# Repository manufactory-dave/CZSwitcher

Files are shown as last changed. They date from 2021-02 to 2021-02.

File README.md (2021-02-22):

# CZSwitcher

====Cube Zero Switcher Project====

Version 1
Board revisions:

Distro Rev 0
Carriage Rev 0
Tool Rev 0

====Overview====

This is the project data store for the Cube Zero custom electronics. Why Cube Zero? Because that film came after Cube 2 Hypercube, and it was a better film.

The Cube Zero is my 3D printer design, essentially a Hypercube/HEVort inspired thing that features a cable-less tool changing system, because outlandish expense and complication is king. My intent is not to have airtight documentation here, as that will kill progress on the project. Please do submit questions via whatever method github suggests best, I have relatively little experience with the platform.

Three seperate KiCad v5 projects are stored here:

Distroboard: The heart of the electronics - this takes a common stepper motor input and 3 separate fan/heater/thermistor channels, bed probing and well as 3 auxilliary channels and routes them to a 20 way 1mm pitch FFC.
Designed to interface with a Bigtreetech GTR V1.0, but will probably work with other boards, YMMV.

*Current Ratings*
Heaters - 3.5A per channel, max 30V
Fans - 1A per channel, routed via Aux 1
Auxilliary channels - 1A per channel, max 24V
Thermistors - currently designed to interface directly with the GTR thermistors. A 3V3 connection is required for at least one thermistor as this supplies power to your Z probe solution of choice.
	Provision has been made to allow these channels to drive thermocouple or PTH amplifiers.
5V in - 1A max
VDC in - 1A max, 30V max
Stepper motor - designed for a TMC2209, with protection circuitry for hot swapping taken from the TMC2209 datasheet. This is not intended and disable stepper commands should be used before swapping motors, however the protection is there just in case.
Probe - low current.

Carriageboard: 3 separate boards.

Carriage Board A:
Breaks out the FFC cable into the 3 aux outputs, a BLTouch connector, an interface for a Precision Piezo V2.85 board and 2 piezo inputs, status LEDs for the heater and probe throughput.

Carriage Board B:
Interfaces with toolhead, provides 2 aux outputs, and repeats status LEDs

LED status board:
For if you need status LEDs somewhere that the above two boards don't help with.

Toolboard: 5 separate boards:
Toolboard A & B ride on the tool, and provide electrical connection to the toolhead and dock. Everything that needs to terminate here to support extruder motors, hot end cooling fans, thermal sense and heating, terminates here.

Dock Interface Board - Takes a high power and data connection from the Distro board, takes a logic input from an external sensor that detects when a tool is removed from the dock and sends it down the data connection to enable that tool over the FFC
Dock LEDs - provides heating and tool select status LEDs for fun/info/making your machine look cool.
Dock Umbilical - connected via FFC to the interface board, provides a mobile connection point to form electrical connections with a docked tool.

====Errors====
There are two known errors:
Carriageboard (no gate resistor on Q2)
Toolboard (Q2 Source and Drain reversed)

====BOM====
The BOM is sketchy, once it's defined and working I'll update it. For now it has several errors and parts I already owned do not have part numbers attached.

====PCBs====
Not available at this time

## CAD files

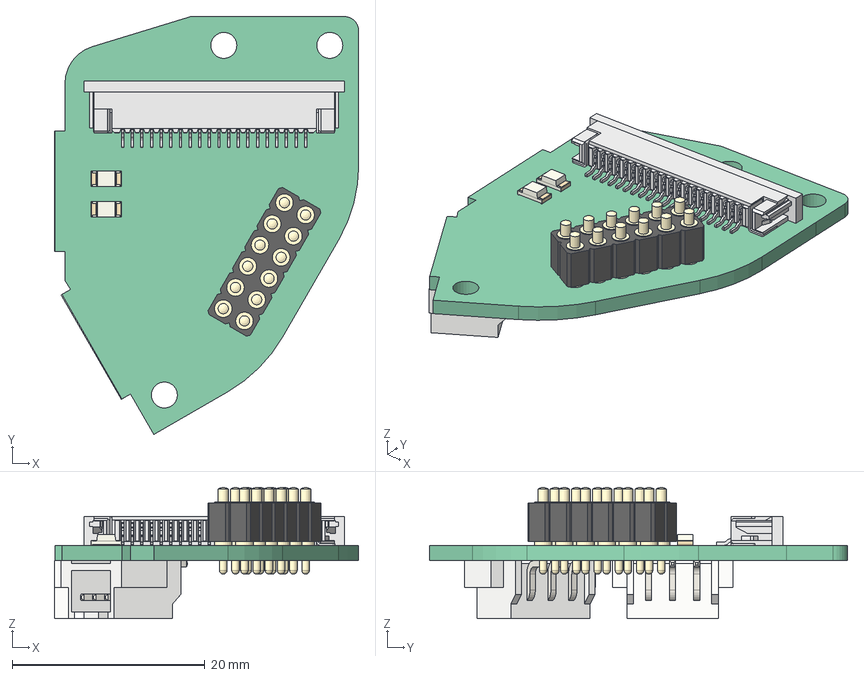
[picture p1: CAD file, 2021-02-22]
carriageboards/toolpost_board_final.step
31.6 x 43.4 x 13.6 mm
Local_CS_be1
Pcb_be1
PCB_Sketch_be1
J14_813-S1-012-10-014_5FF84852
J11_ZF1-20-01-T-WT-TR001_5FFBF43E
D6_LED_1206_3216Metric_5FFBFFB6 x 2
J12_JST-XH_SMT_1x3_5FFBF74F x 2

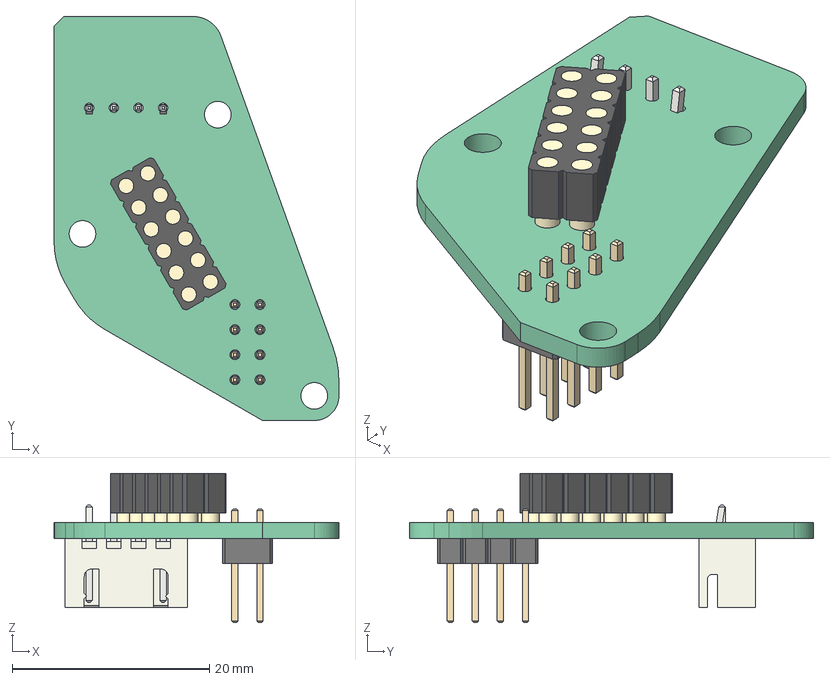
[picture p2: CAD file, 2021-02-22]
toolboards/toolhead_interface_pcb_v1.step
28.9 x 41.0 x 15.1 mm
Local_CS_7721
Pcb_7721
PCB_Sketch_7721
J0_802-10-012-30-507101_60049A0C
J1_JST_B4B_XH_A_5FFDFDDD
J2_PinHeader_2x04_P254mm_Vertical_6002294E

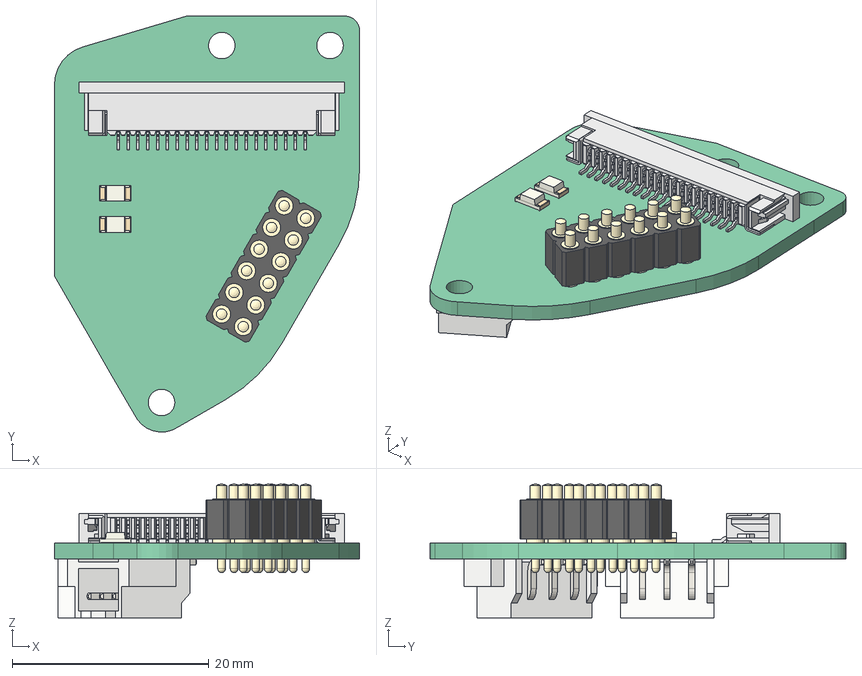
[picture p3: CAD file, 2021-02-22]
carriageboards/toolpost_board_v1.step
31.0 x 42.3 x 13.6 mm
Local_CS_be1
Pcb_be1
PCB_Sketch_be1
J14_813-S1-012-10-014_5FF84852
J11_ZF1-20-01-T-WT-TR001_5FFBF43E
D6_LED_1206_3216Metric_5FFBFFB6 x 2
J12_JST-XH_SMT_1x3_5FFBF74F x 2

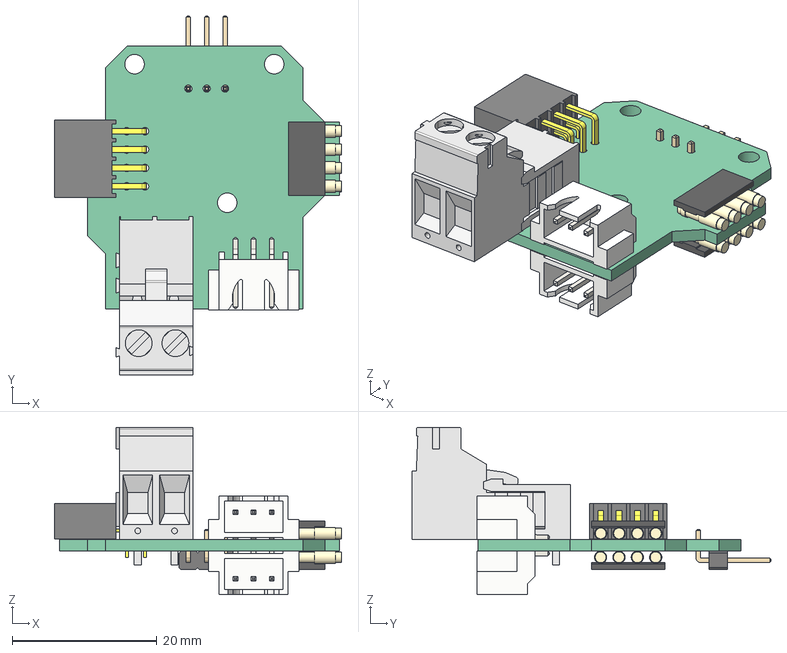
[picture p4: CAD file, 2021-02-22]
toolboards/toolhead_plug_pcb_v10.step
39.7 x 49.6 x 23.1 mm
Local_CS_6657
Pcb_6657
PCB_Sketch_6657
J3_ssw-104-02-g-d-ra_6009D480
J8_8MM-11-004-02-131_600C5BE0 x 2
J5_C-282815-2_600C5B60
J5_C-282807-2_600C5B60[2]
J6_JST-XH_SMT_1x3_6009D3B3 x 2
JP0_PinHeader_1x03_P254mm_Horizontal_6009D4DE

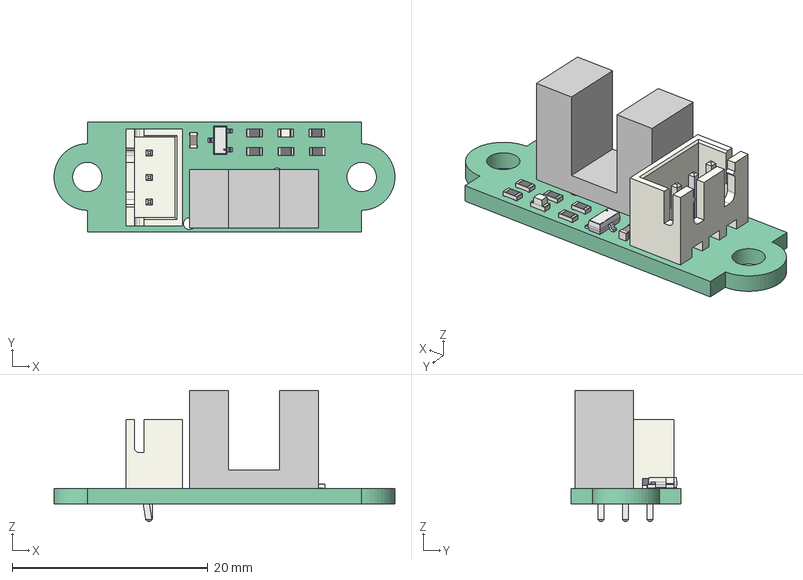
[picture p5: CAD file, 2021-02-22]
toolboards/opto_endstop.step
34.8 x 11.2 x 13.4 mm
Local_CS_877e
Pcb_877e
PCB_Sketch_877e
U1_Opto_Switch_60112675
R5_R_0603_1608Metric_60112659 x 5
Q1_FDV304P_60112A24
J1_JST_B3B_XH_A_601125EE
D1_LED_0603_1608Metric_60112815
C1_C_0603_1608Metric_601129B8

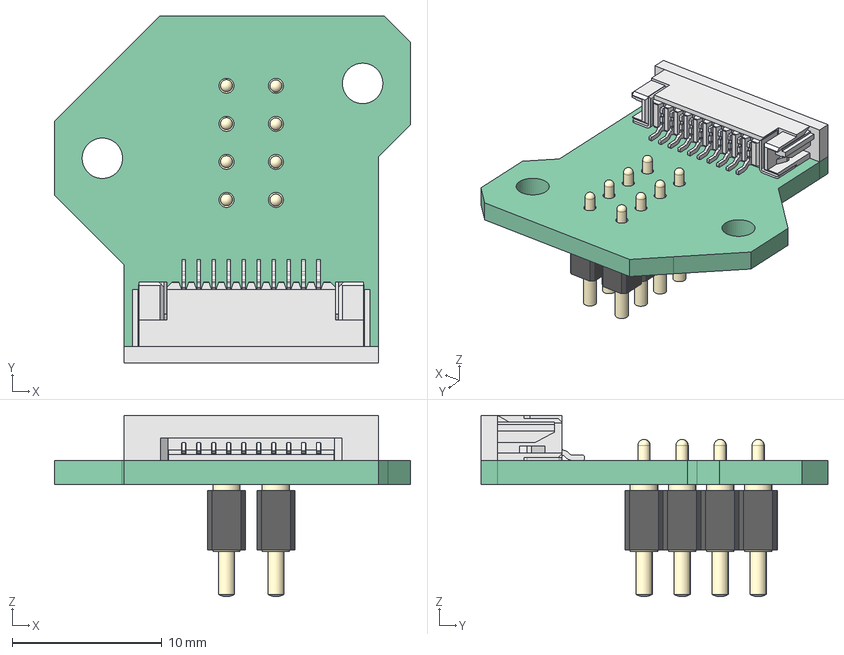
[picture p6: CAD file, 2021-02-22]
toolboards/umbilical_pcb_v5.step
23.8 x 23.2 x 12.1 mm
Local_CS_6006
Pcb_6006
PCB_Sketch_6006
J10_ZF1-10-01-T-WT-TR001_60089AD0
J11_811-S1-004-10-017_600CD6DF x 2

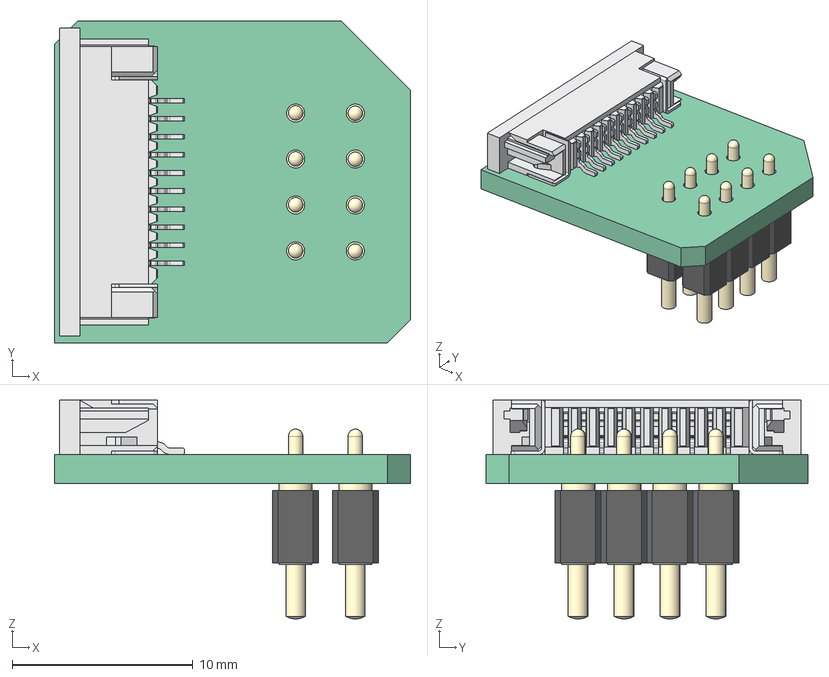
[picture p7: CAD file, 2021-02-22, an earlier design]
toolboards/umbilical_pcb_v3.step
19.7 x 17.8 x 12.1 mm
Local_CS_c0
Pcb_c0
PCB_Sketch_c0
J10_ZF1-10-01-T-WT-TR001_60089AD0
J11_811-S1-004-10-017_600CD6DF x 2

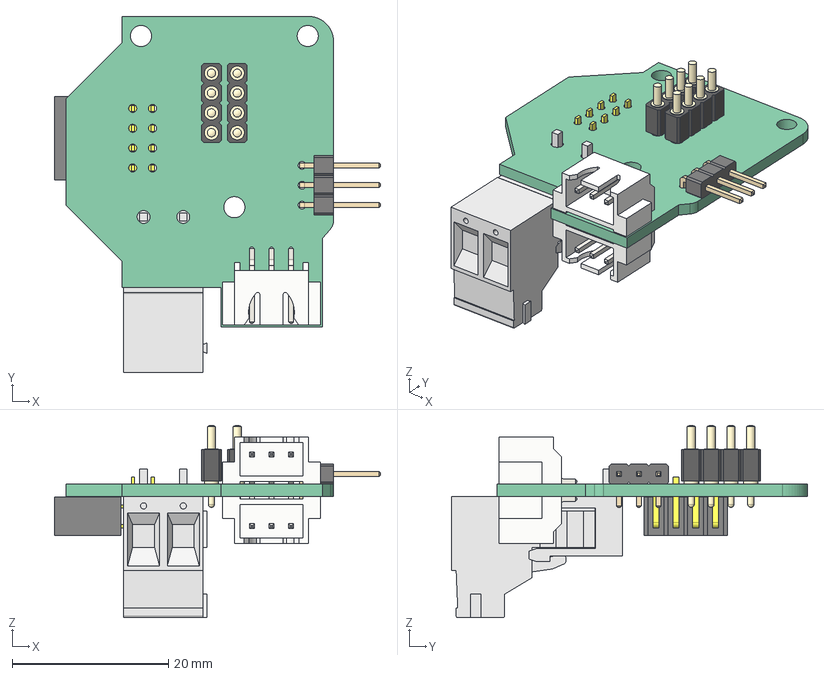
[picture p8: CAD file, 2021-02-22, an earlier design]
toolboards/toolhead_plug_pcb_v1.step
41.7 x 45.6 x 24.6 mm
Local_CS_4742
Pcb_4742
PCB_Sketch_4742
J8_811-S1-004-10-017_6005AF96 x 2
JP0_PinHeader_1x03_P254mm_Horizontal_6005AD56
J4_JST-XH_SMT_1x3_6005AE06 x 2
J3_ssw-104-02-g-d-ra_6005AFCC
J5_C-282815-2_6005AF65
J5_C-282807-2_6005AF65[2]

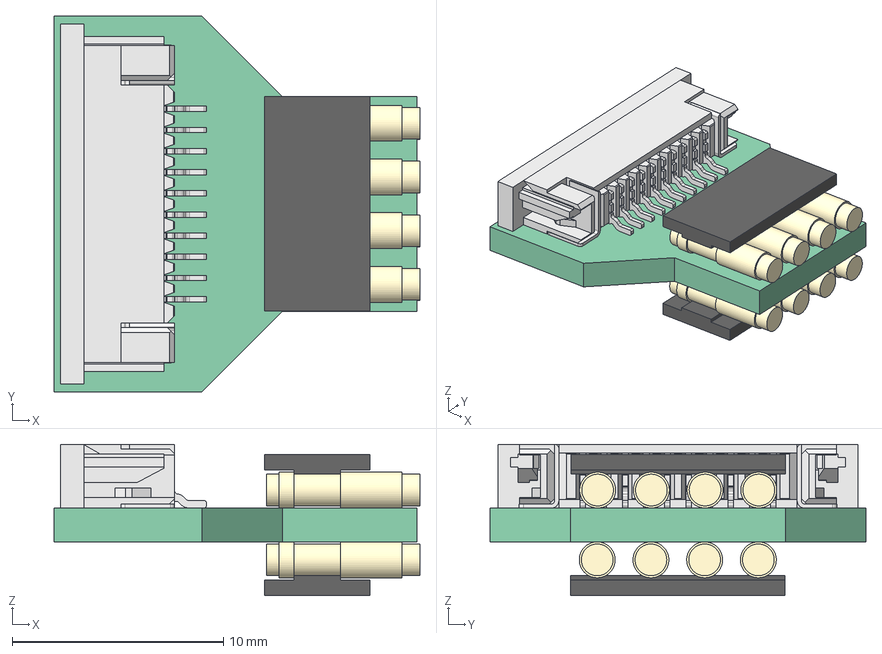
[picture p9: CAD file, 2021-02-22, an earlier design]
toolboards/umbilical_pcb_v2.step
17.3 x 17.8 x 7.15 mm
Local_CS_10e1
Pcb_10e1
PCB_Sketch_10e1
J10_ZF1-10-01-T-WT-TR001_60089AD0
J9_8MM-11-004-02-131_600627A0 x 2

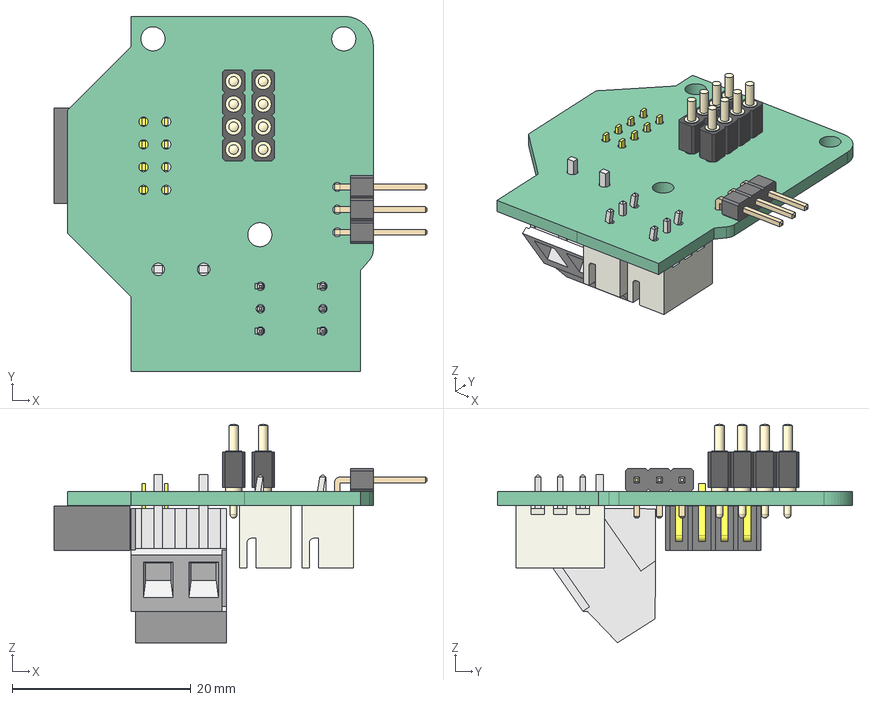
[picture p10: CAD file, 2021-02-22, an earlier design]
toolboards/toolhead_plug_pcb_v3.step
41.7 x 39.7 x 24.4 mm
Local_CS_25a3
Pcb_25a3
PCB_Sketch_25a3
JP0_PinHeader_1x03_P254mm_Horizontal_6005AD56
J8_811-S1-004-10-017_6005AF96 x 2
J5_C-282847-2_6005AF65
J6_JST_B3B_XH_A_60053BFE x 2
J3_ssw-104-02-g-d-ra_6005AFCC

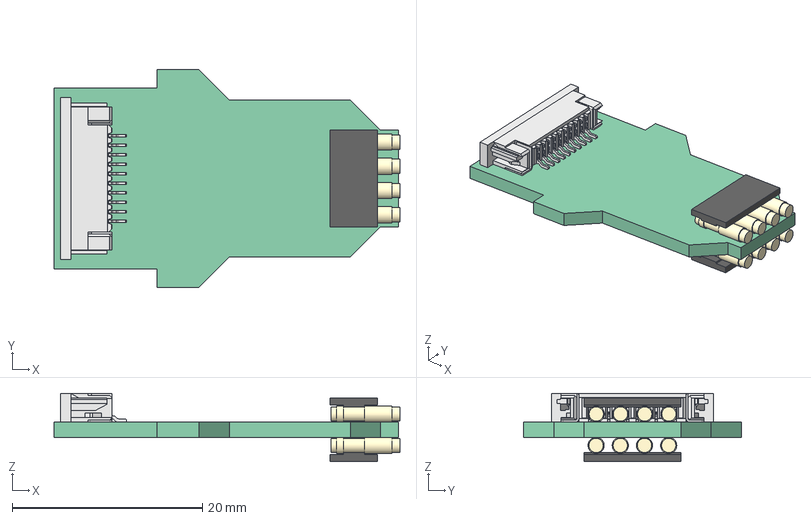
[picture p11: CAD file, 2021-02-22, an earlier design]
toolboards/umbilical_pcb_v1.step
36.3 x 22.9 x 7.15 mm
Local_CS_2082
Pcb_2082
PCB_Sketch_2082
J10_ZF1-10-01-T-WT-TR001_600627BD
J11_8MM-11-004-02-131_60063E7D x 2

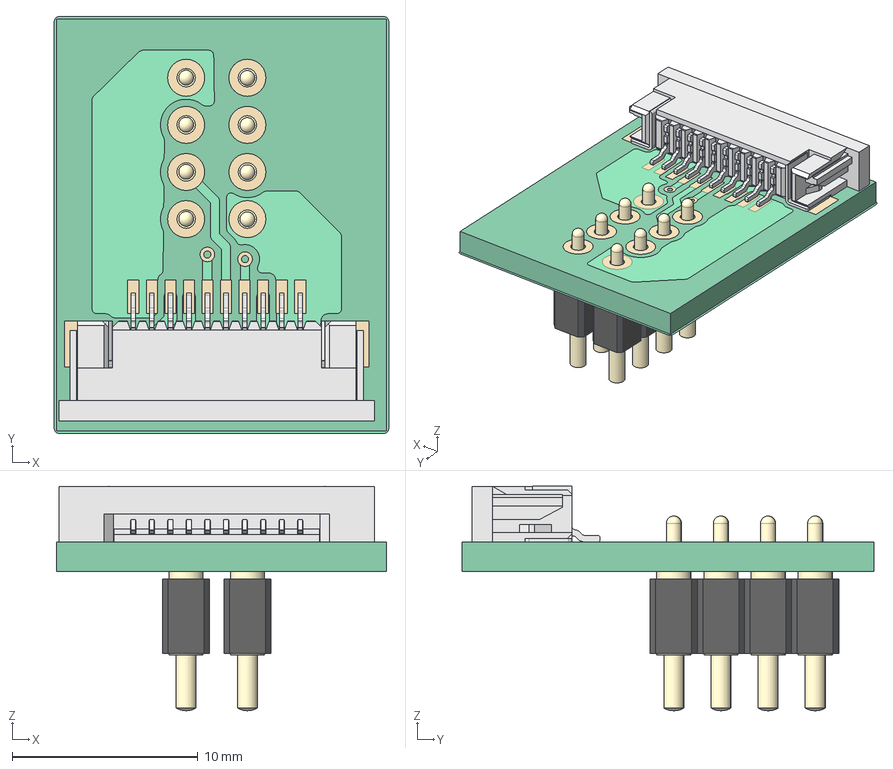
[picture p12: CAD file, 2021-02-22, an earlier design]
toolboards/umbilical_pcb_v4.step
18.0 x 22.5 x 12.1 mm
Local_CS_7027
Pcb_7027
PCB_Sketch_7027
topTracks_7027
botTracks_7027
J10_ZF1-10-01-T-WT-TR001_60089AD0
J11_811-S1-004-10-017_600CD6DF x 2

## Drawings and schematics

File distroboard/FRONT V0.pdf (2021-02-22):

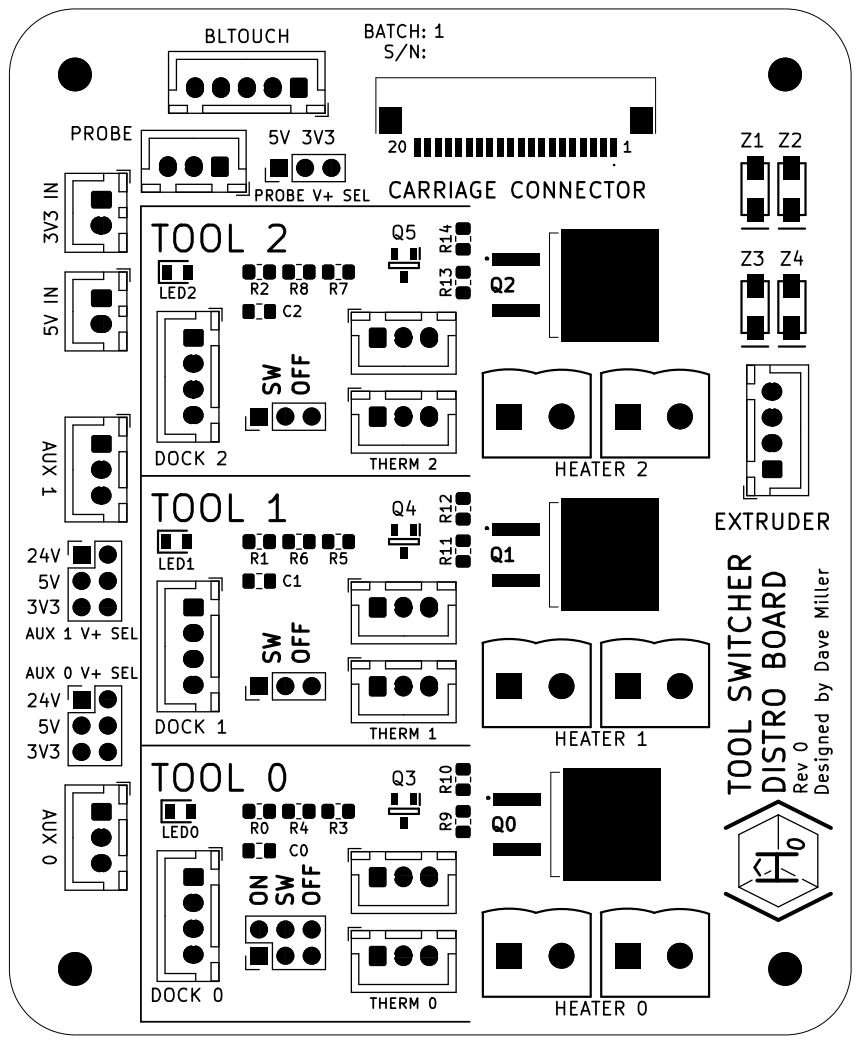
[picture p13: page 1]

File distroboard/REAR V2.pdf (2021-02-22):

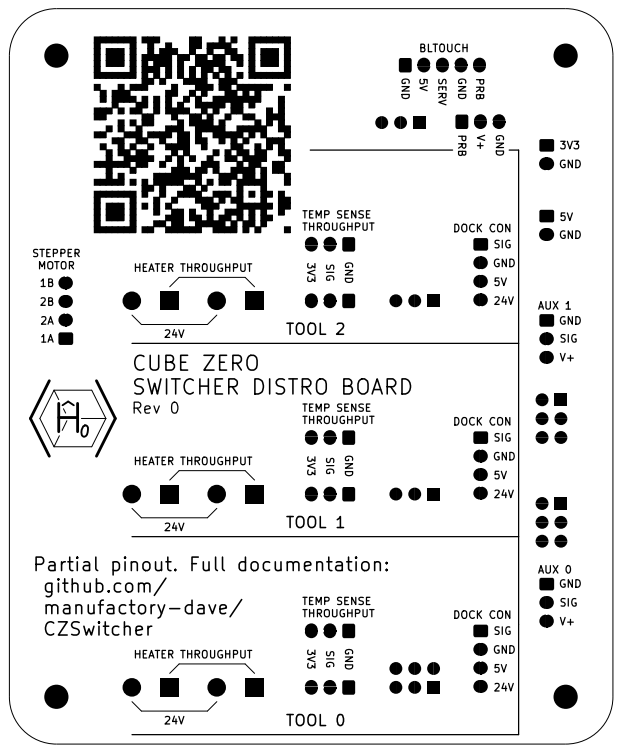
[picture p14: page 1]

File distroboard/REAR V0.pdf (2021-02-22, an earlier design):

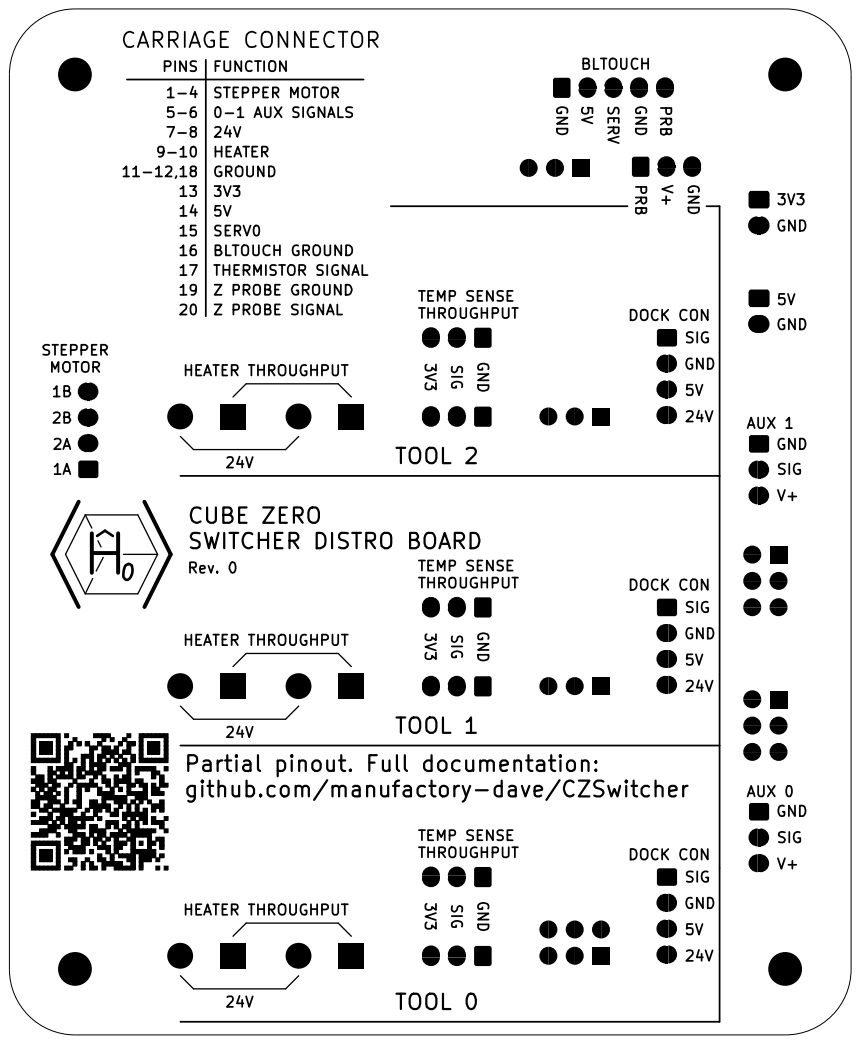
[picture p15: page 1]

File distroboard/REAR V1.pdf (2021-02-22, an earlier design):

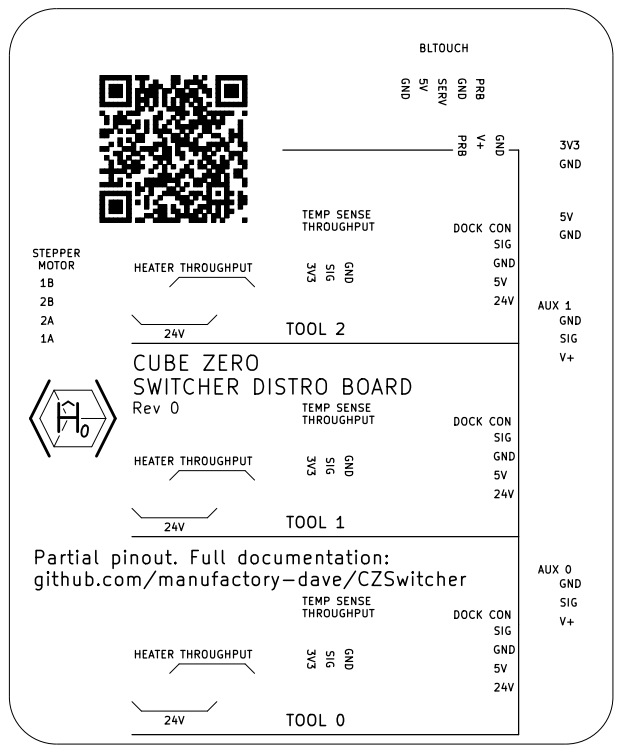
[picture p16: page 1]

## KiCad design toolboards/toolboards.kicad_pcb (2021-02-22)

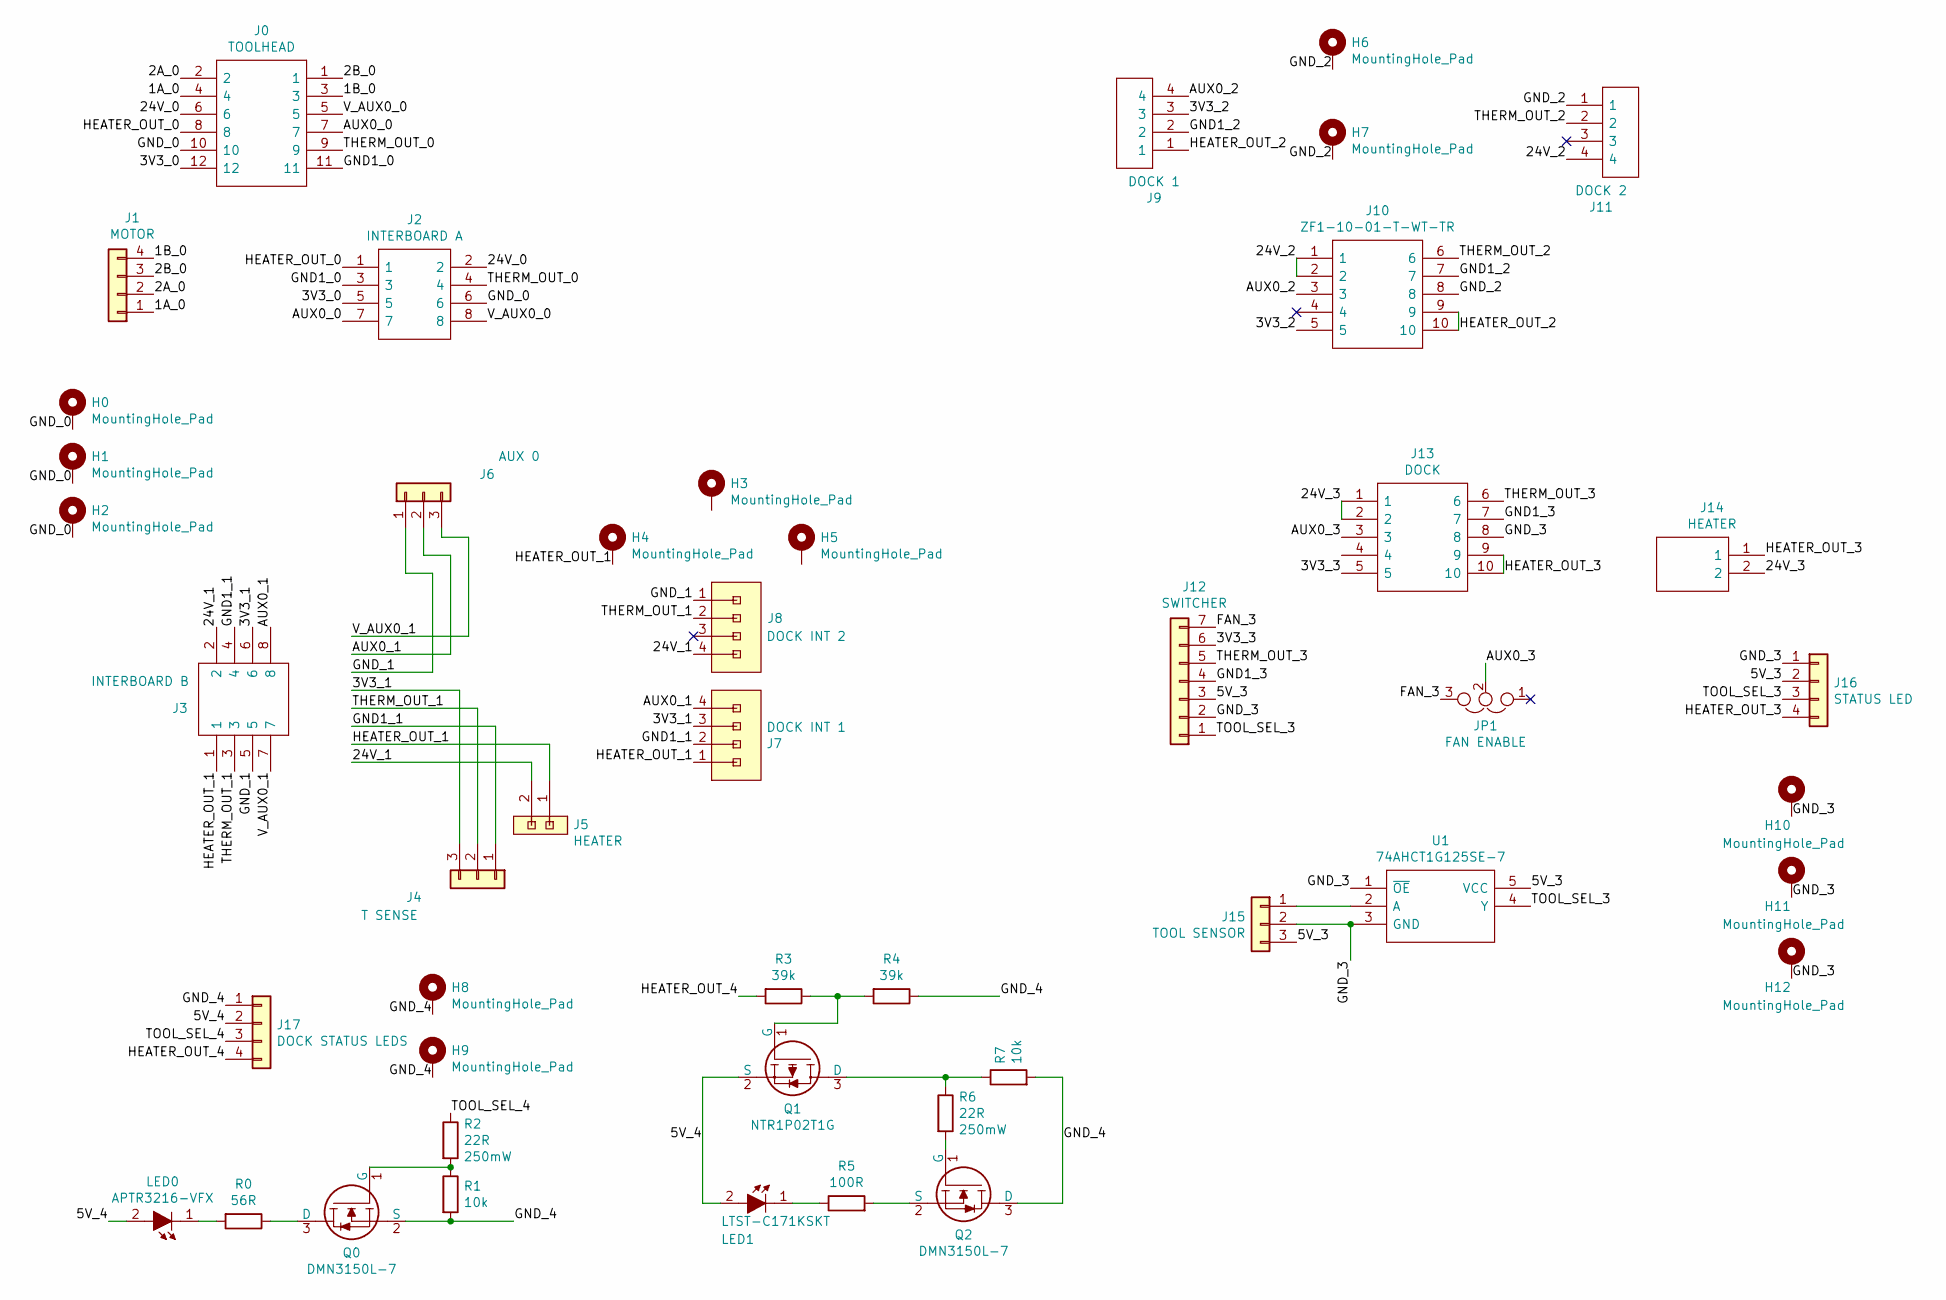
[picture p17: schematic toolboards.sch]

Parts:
H0, H1, H2, H3, H4, H5: MountingHole_Pad; MountingHole_2.7mm_M2.5_DIN965_Pad_TopBottom
H6, H7, H8, H9, H10, H11, H12: MountingHole_Pad; MountingHole_3.2mm_M3_DIN965_Pad_TopBottom
J0: TOOLHEAD; 8021001230507101_HS; Manufacturer_Part_Number 802-10-012-30-507101
J1: MOTOR; JST_XH_B4B-XH-A_1x04_P2.50mm_Vertical
J2: INTERBOARD A; HDRV8W64P254_2X4_1016X495X838P; Manufacturer_Part_Number TSW-104-07-T-D
J3: INTERBOARD B; SSW-104-XX-YYY-D-RA; Manufacturer_Part_Number SSW-104-02-T-D-RA
J4: T SENSE; JST-XH_2.50MM_03x01_SMT; Manufacturer_Part_Number S3B-XH-SM4-TB(LF)(SN)
J5, J14: HEATER; SHDRRA2W102P0X508_1X2_1016X1200X850P; Manufacturer_Part_Number 282815-2
J6: AUX 0; JST-XH_2.50MM_03x01_SMT; Manufacturer_Part_Number S3B-XH-SM4-TB(LF)(SN)
J7: DOCK INT 1; 8MM11000402131_handsolder
J8: DOCK INT 2; 8MM11000402131_handsolder
J9: DOCK 1; 811-S1-004-10-017101; Mouser Part Number 437-8MM11000402131
J10: ZF1-10-01-T-WT-TR; ZF1-10-XX-ZZ-WT_Handsolder; Manufacturer_Part_Number ZF1-10-01-T-WT-TR
J11: DOCK 2; 811-S1-004-10-017101; Mouser Part Number 437-8MM11000402131
J12: SWITCHER; JST_XH_B7B-XH-A_1x07_P2.50mm_Vertical
J13: DOCK; ZF1-10-XX-ZZ-WT_Handsolder; Manufacturer_Part_Number ZF1-10-01-T-WT-TR
J15: TOOL SENSOR; JST_XH_B3B-XH-A_1x03_P2.50mm_Vertical
J16: STATUS LED; JST-ZH_S4B-ZR-SM4A-TF; Part Number S4B-ZR-SM4A-TF
J17: DOCK STATUS LEDS; JST-ZH_S4B-ZR-SM4A-TF; Part Number S4B-ZR-SM4A-TF
JP1: FAN ENABLE; PinHeader_1x03_P2.54mm_Vertical
LED0: APTR3216-VFX; LED_1206_3216Metric_Pad1.42x1.75mm_HandSolder; Manufacturer_Part_Number APTR3216-VFX
LED1: LTST-C171KSKT; LED_0805_2012Metric_Pad1.15x1.40mm_HandSolder; Manufacturer_Part_Number LTST-C171KSKT
Q0, Q2: DMN3150L-7; SUPER-SOT-3; Manufacturer_Part_Number DMN3150L-7
Q1: NTR1P02T1G; SUPER-SOT-3; Manufacturer_Part_Number NTR1P02T1G
R0: 56R; R_0805_2012Metric_Pad1.20x1.40mm_HandSolder; Manufacturer_Part_Number RK73B2ATTD560J
R1, R7: 10k; R_0805_2012Metric_Pad1.20x1.40mm_HandSolder; Manufacturer_Part_Number RK73B2ATTE103J
R2, R6: 22R; R_0805_2012Metric_Pad1.20x1.40mm_HandSolder; Manufacturer_Part_Number RK73B2ATTDD220J
R3: 39k; R_0805_2012Metric_Pad1.20x1.40mm_HandSolder; Manufacturer_Part_Number RK73B2ATTE393J
R4: 39k; R_0805_2012Metric_Pad1.20x1.40mm_HandSolder; Manufacturer_Part_Number RK73B2ATTE103J
R5: 100R; R_0805_2012Metric_Pad1.20x1.40mm_HandSolder; Manufacturer_Part_Number RK73B2ATTE101J
U1: 74AHCT1G125SE-7; SOT-23-5_HandSoldering; Manufacturer_Part_Number 74AHCT1G125SE-7

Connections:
/1A_0: J0.4, J1.1
/1B_0: J0.3, J1.4
/2A_0: J0.2, J1.2
/2B_0: J0.1, J1.3
/3V3_0: J0.12, J2.5
/3V3_1: J3.6, J4.3, J7.3
/3V3_2: J9.3, J10.5
/3V3_3: J12.6, J13.5
/5V_3: J12.3, J15.3, J16.2, U1.5 (VCC)
/5V_4: J17.2, LED0.2, LED1.2, Q1.2 (S)
/24V_0: J0.6, J2.2
/24V_1: J3.2, J4.4, J4.5, J5.2, J8.4
/24V_2: J10.1, J10.2, J11.4
/24V_3: J13.1, J13.2, J14.2
/AUX0_0: J0.7, J2.7
/AUX0_1: J3.8, J6.2, J7.4
/AUX0_2: J9.4, J10.3
/AUX0_3: J13.3, JP1.2
/FAN_3: J12.7, JP1.3
/GND1_0: J0.11, J2.3
/GND1_1: J3.4, J4.1, J7.2
/GND1_2: J9.2, J10.7
/GND1_3: J12.4, J13.7
/GND_0: H0.1, H1.1, H2.1, J0.10, J2.6
/GND_1: J3.5, J6.1, J8.1
/GND_2: H6.1, H7.1, J10.8, J10.11, J10.12, J11.1
/GND_3: H10.1, H11.1, H12.1, J12.2, J13.8, J15.2, J16.1, U1.1 (~OE), U1.3 (GND)
/GND_4: H8.1, H9.1, J17.1, Q0.2 (S), Q2.3 (D), R1.2, R4.1, R7.2
/HEATER_OUT_0: J0.8, J2.1
/HEATER_OUT_1: H4.1, J3.1, J5.1, J7.1
/HEATER_OUT_2: J9.1, J10.9, J10.10
/HEATER_OUT_3: J13.9, J13.10, J14.1, J16.4
/HEATER_OUT_4: J17.4, R3.2
/THERM_OUT_0: J0.9, J2.4
/THERM_OUT_1: J3.3, J4.2, J8.2
/THERM_OUT_2: J10.6, J11.2
/THERM_OUT_3: J12.5, J13.6
/TOOL_SEL_3: J12.1, J16.3, U1.4 (Y)
/TOOL_SEL_4: J17.3, R2.1
/V_AUX0_0: J0.5, J2.8
/V_AUX0_1: J3.7, J6.3
unnamed: J15.1, U1.2 (A)
unnamed: LED0.1, R0.2
unnamed: LED1.1, R5.1
unnamed: Q0.1 (G), R1.1, R2.2
unnamed: Q0.3 (D), R0.1
unnamed: Q1.1 (G), R3.1, R4.2
unnamed: Q1.3 (D), R6.1, R7.1
unnamed: Q2.1 (G), R6.2
unnamed: Q2.2 (S), R5.2

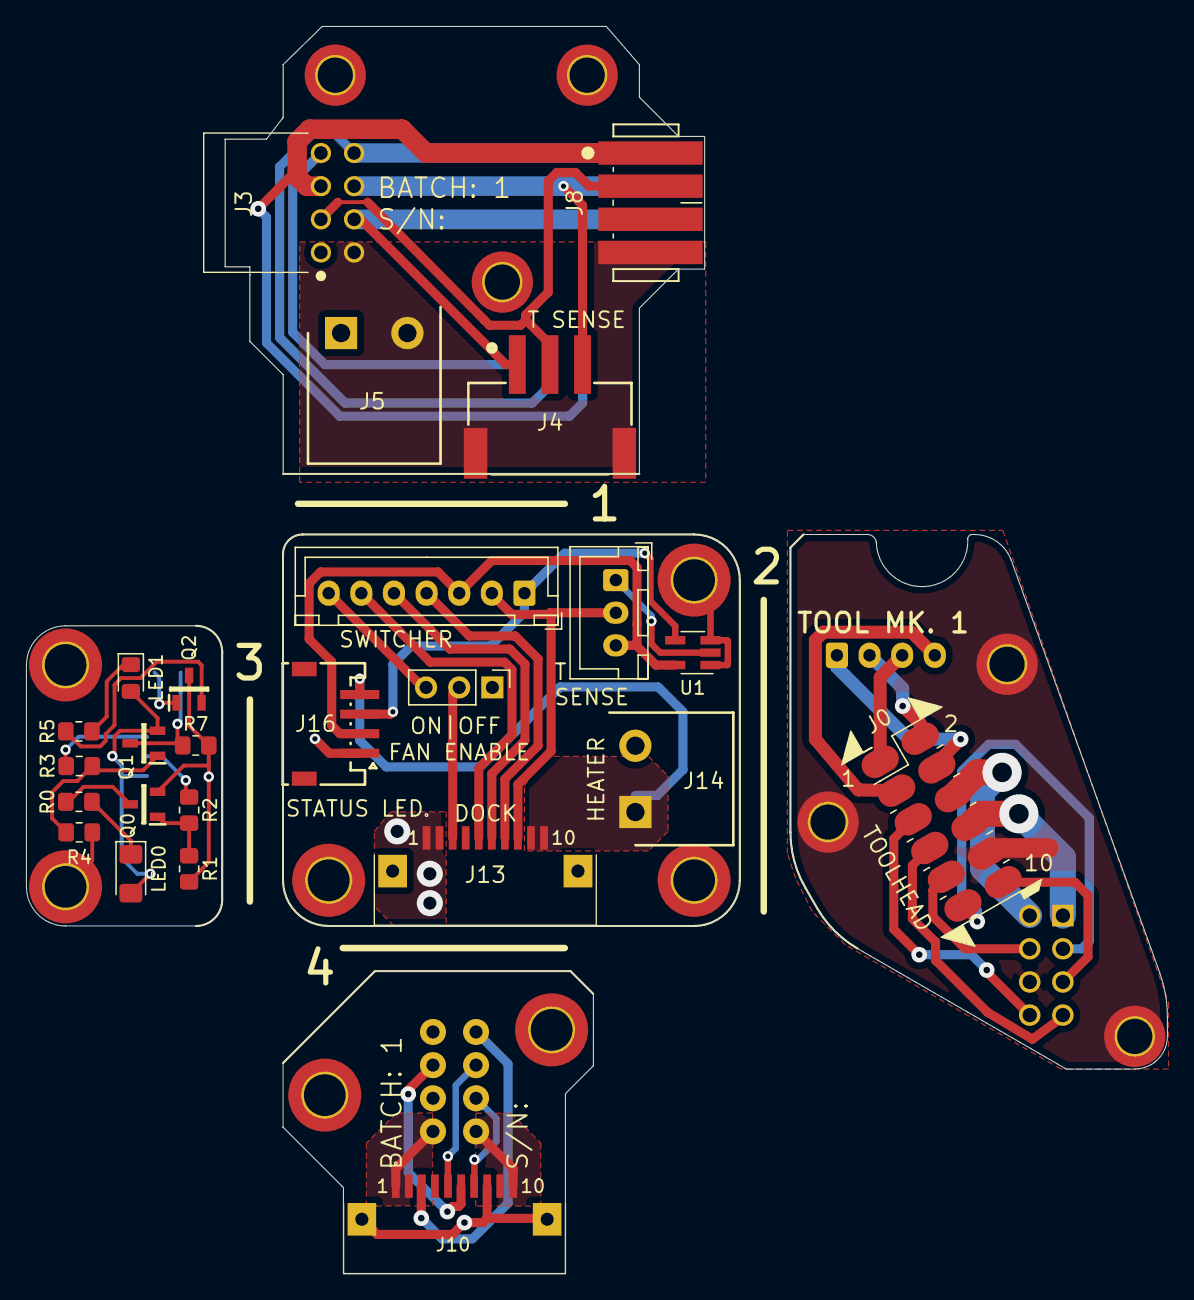
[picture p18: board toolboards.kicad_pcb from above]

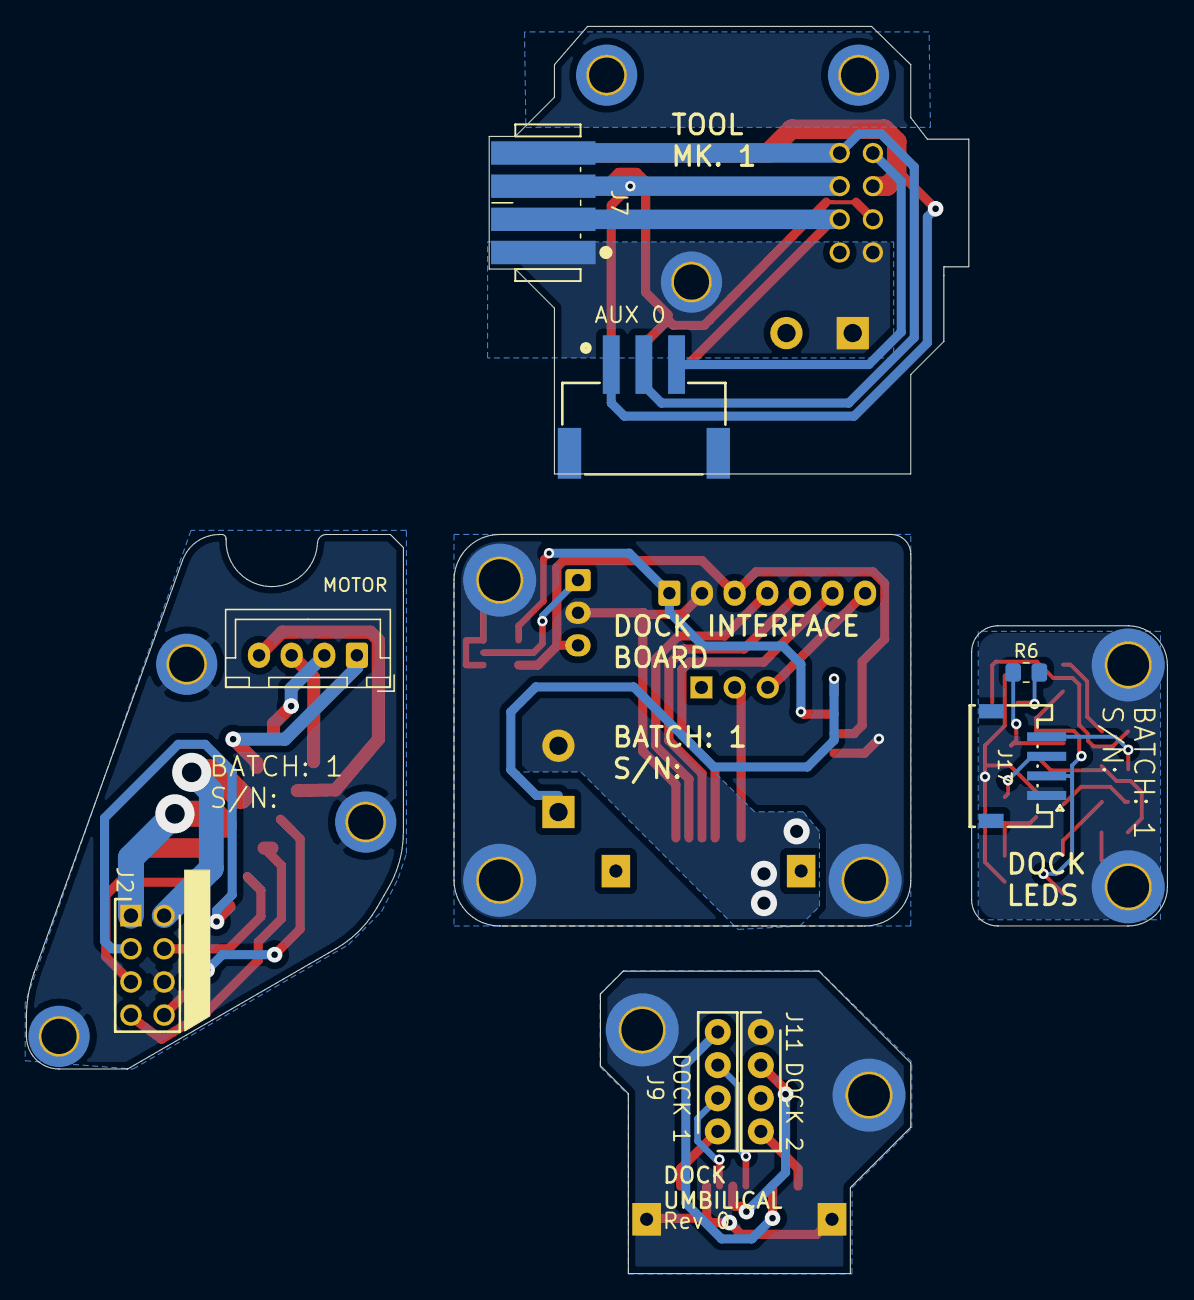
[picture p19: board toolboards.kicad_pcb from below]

Board: 2 copper layers, 87.4 x 95.6 mm, 46 parts (8 on the bottom side), 50 nets.

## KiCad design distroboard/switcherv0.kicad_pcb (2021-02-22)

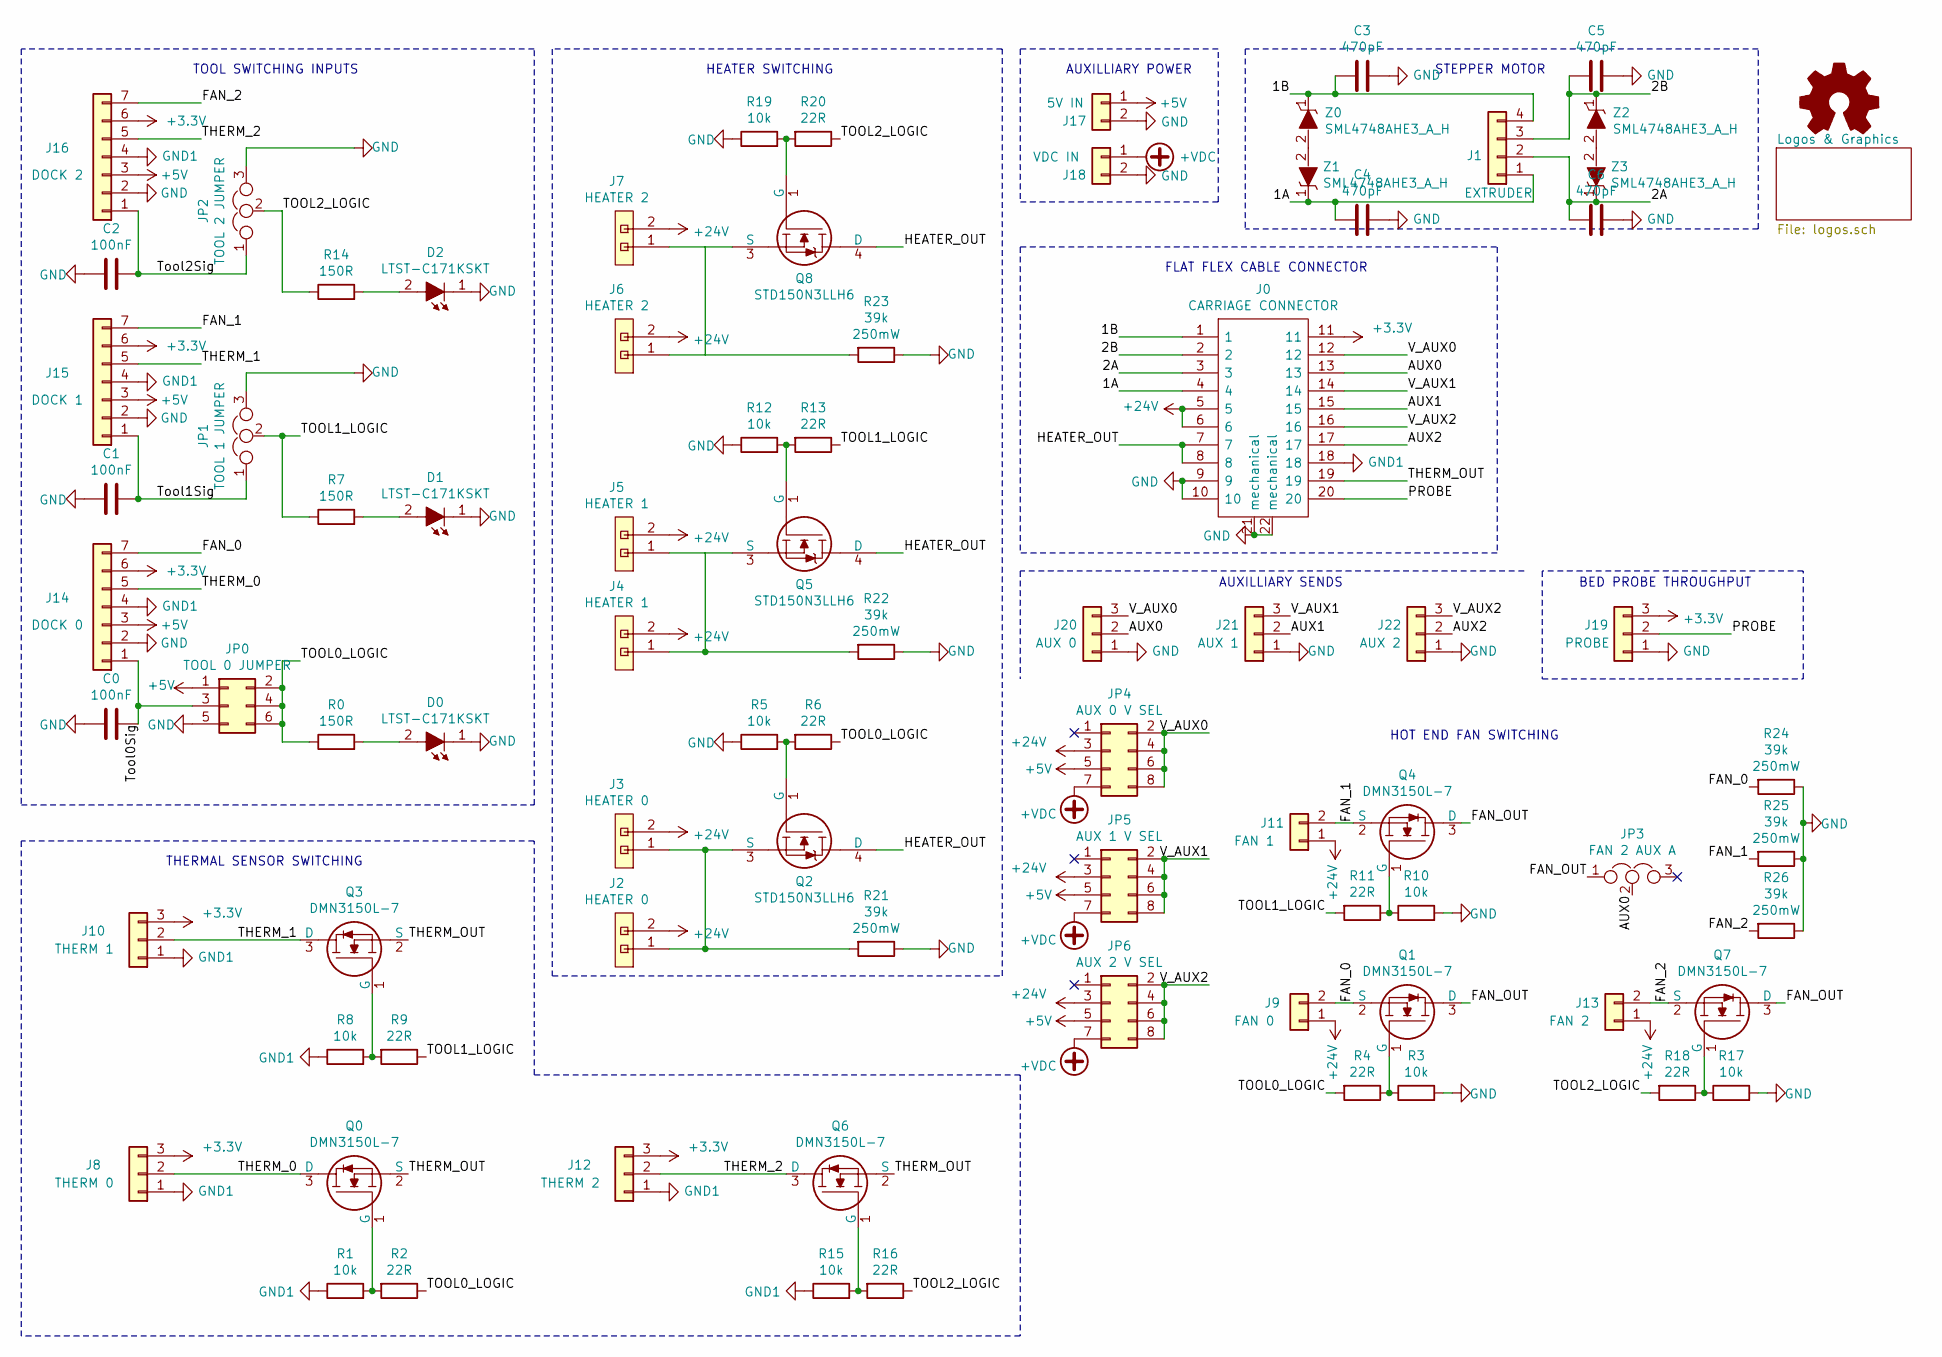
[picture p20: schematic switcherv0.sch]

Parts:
C0, C1, C2: 100nF; C_0805_2012Metric_Pad1.18x1.45mm_HandSolder; Manufacturer_Part_Number 08051C103KAT2A
C3, C4, C5, C6: 470pF; C_0805_2012Metric_Pad1.18x1.45mm_HandSolder; Manufacturer_Part_Number C0805C471J1GACTU
D0, D1, D2: LTST-C171KSKT; LED_0805_2012Metric_Pad1.15x1.40mm_HandSolder; Manufacturer_Part_Number LTST-C171KSKT
J0: CARRIAGE CONNECTOR; ZF1-20-XX-ZZ-WT; Manufacturer_Part_Number ZF1-20-01-T-WT
J1: EXTRUDER; JST_XH_B4B-XH-A_1x04_P2.50mm_Vertical
J2, J3: HEATER 0; SHDR2W102P0X508_1X2_1016X835X1230P; Manufacturer_Part_Number 282824-2
J4, J5: HEATER 1; SHDR2W102P0X508_1X2_1016X835X1230P; Manufacturer_Part_Number 282824-2
J6, J7: HEATER 2; SHDR2W102P0X508_1X2_1016X835X1230P; Manufacturer_Part_Number 282824-2
J8: THERM 0; JST_XH_B3B-XH-A_1x03_P2.50mm_Vertical
J9: FAN 0; JST_XH_B2B-XH-A_1x02_P2.50mm_Vertical
J10: THERM 1; JST_XH_B3B-XH-A_1x03_P2.50mm_Vertical
J11: FAN 1; JST_XH_B2B-XH-A_1x02_P2.50mm_Vertical
J12: THERM 2; JST_XH_B3B-XH-A_1x03_P2.50mm_Vertical
J13: FAN 2; JST_XH_B2B-XH-A_1x02_P2.50mm_Vertical
J14: DOCK 0; JST_XH_B7B-XH-A_1x07_P2.50mm_Vertical
J15: DOCK 1; JST_XH_B7B-XH-A_1x07_P2.50mm_Vertical
J16: DOCK 2; JST_XH_B7B-XH-A_1x07_P2.50mm_Vertical
J17: 5V IN; JST_XH_B2B-XH-A_1x02_P2.50mm_Vertical
J18: VDC IN; JST_XH_B2B-XH-A_1x02_P2.50mm_Vertical
J19: PROBE; JST_XH_B3B-XH-A_1x03_P2.50mm_Vertical
J20: AUX 0; JST_XH_B3B-XH-A_1x03_P2.50mm_Vertical
J21: AUX 1; JST_XH_B3B-XH-A_1x03_P2.50mm_Vertical
J22: AUX 2; JST_XH_B3B-XH-A_1x03_P2.50mm_Vertical
JP0: TOOL 0 JUMPER; PinHeader_2x03_P2.54mm_Vertical
JP1: TOOL 1 JUMPER; PinHeader_1x03_P2.54mm_Vertical
JP2: TOOL 2 JUMPER; PinHeader_1x03_P2.54mm_Vertical
JP3: FAN 2 AUX A; PinHeader_1x03_P2.54mm_Vertical
JP4: AUX 0 V SEL; PinHeader_2x04_P1.27mm_Vertical; Manufacturer_Part_Number M50-055023W0445
JP5: AUX 1 V SEL; PinHeader_2x04_P1.27mm_Vertical; Manufacturer_Part_Number M50-055023W0445
JP6: AUX 2 V SEL; PinHeader_2x04_P1.27mm_Vertical; Manufacturer_Part_Number M50-055023W0445
LOGO2: Logo_Open_Hardware_Small; OSHW-Symbol_8.9x8mm_Copper
Q0, Q1, Q3, Q4, Q6, Q7: DMN3150L-7; SUPER-SOT-3; Manufacturer_Part_Number DMN3150L-7
Q2, Q5, Q8: STD150N3LLH6; TO228P972X240-3N; Manufacturer_Part_Number STD150N3LLH6
R0, R7, R14: 150R; R_0805_2012Metric_Pad1.20x1.40mm_HandSolder; Manufacturer_Part_Number RK73B2ATTE151J
R1, R3, R5, R8, R10, R12, R15, R17, R19: 10k; R_0805_2012Metric_Pad1.20x1.40mm_HandSolder; Manufacturer_Part_Number RK73B2ATTE103J
R2, R4, R6, R9, R11, R13, R16, R18, R20: 22R; R_0805_2012Metric_Pad1.20x1.40mm_HandSolder; Manufacturer_Part_Number RK73B2ATTDD220J
R21, R22, R23, R24, R25, R26: 39k; R_0805_2012Metric_Pad1.20x1.40mm_HandSolder; Manufacturer_Part_Number RK73B2ATTD393J
Z0, Z1, Z2, Z3: SML4748AHE3_A_H; DIOM5127X229N; Mouser Part Number 78-SML4748AHE3_A/H

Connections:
+3V3: J0.11, J8.3, J10.3, J12.3, J14.6, J15.6, J16.6, J19.3
+5V: J14.3, J15.3, J16.3, J17.1, JP0.1, JP4.5, JP5.5, JP6.5
+24V: J0.5, J0.6, J2.2, J3.2, J4.2, J5.2, J6.2, J7.2, J9.1, J11.1, J13.1, JP4.3, JP5.3, JP6.3
+VDC: J18.1, JP4.7, JP5.7, JP6.7
/1A: C4.2, J0.4, J1.1, Z1.1
/1B: C3.2, J0.1, J1.4, Z0.1
/2A: C6.2, J0.3, J1.2, Z3.1
/2B: C5.2, J0.2, J1.3, Z2.1
/AUX0: J0.13, J20.2, JP3.2
/AUX1: J0.15, J21.2
/AUX2: J0.17, J22.2
/FAN_0: J9.2, J14.7, Q1.2 (S), R24.2
/FAN_1: J11.2, J15.7, Q4.2 (S), R25.2
/FAN_2: J13.2, J16.7, Q7.2 (S), R26.2
/FAN_OUT: JP3.1, Q1.3 (D), Q4.3 (D), Q7.3 (D)
/HEATER_OUT: J0.7, J0.8, Q2.4 (D), Q5.4 (D), Q8.4 (D)
/PROBE: J0.20, J19.2
/THERM_0: J8.2, J14.5, Q0.3 (D)
/THERM_1: J10.2, J15.5, Q3.3 (D)
/THERM_2: J12.2, J16.5, Q6.3 (D)
/THERM_OUT: J0.19, Q0.2 (S), Q3.2 (S), Q6.2 (S)
/TOOL0_LOGIC: JP0.2, JP0.4, JP0.6, R0.1, R2.1, R4.2, R6.1
/TOOL1_LOGIC: JP1.2, R7.1, R9.1, R11.2, R13.1
/TOOL2_LOGIC: JP2.2, R14.1, R16.1, R18.2, R20.1
/Tool0Sig: C0.1, J14.1, JP0.3
/Tool1Sig: C1.1, J15.1, JP1.1
/Tool2Sig: C2.1, J16.1, JP2.1
/V_AUX0: J0.12, J20.3, JP4.2, JP4.4, JP4.6, JP4.8
/V_AUX1: J0.14, J21.3, JP5.2, JP5.4, JP5.6, JP5.8
/V_AUX2: J0.16, J22.3, JP6.2, JP6.4, JP6.6, JP6.8
GND: C0.2, C1.2, C2.2, C3.1, C4.1, C5.1, C6.1, D0.1, D1.1, D2.1, J0.9, J0.10, J0.21 (mechanical), J0.22 (mechanical), J14.2, J15.2, J16.2, J17.2, J18.2, J19.1, J20.1, J21.1, J22.1, JP0.5, JP1.3, JP2.3, R3.2, R5.1, R10.2, R12.1, R17.2, R19.1, R21.1, R22.1, R23.1, R24.1, R25.1, R26.1; also elsewhere on the board
GND1: J0.18, J8.1, J10.1, J12.1, J14.4, J15.4, J16.4, R1.1, R8.1, R15.1
unnamed: D0.2, R0.2
unnamed: D1.2, R7.2
unnamed: D2.2, R14.2
unnamed: J2.1, J3.1, Q2.3 (S), R21.2
unnamed: J4.1, J5.1, Q5.3 (S), R22.2
unnamed: J6.1, J7.1, Q8.3 (S), R23.2
unnamed: Q0.1 (G), R1.2, R2.2
unnamed: Q1.1 (G), R3.1, R4.1
unnamed: Q2.1 (G), R5.2, R6.2
unnamed: Q3.1 (G), R8.2, R9.2
unnamed: Q4.1 (G), R10.1, R11.1
unnamed: Q5.1 (G), R12.2, R13.2
unnamed: Q6.1 (G), R15.2, R16.2
unnamed: Q7.1 (G), R17.1, R18.1
unnamed: Q8.1 (G), R19.2, R20.2
unnamed: Z0.2, Z1.2
unnamed: Z2.2, Z3.2

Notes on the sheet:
TOOL SWITCHING INPUTS
HEATER SWITCHING
THERMAL SENSOR SWITCHING
AUXILLIARY POWER
FLAT FLEX CABLE CONNECTOR
AUXILLIARY SENDS
BED PROBE THROUGHPUT
HOT END FAN SWITCHING
STEPPER MOTOR

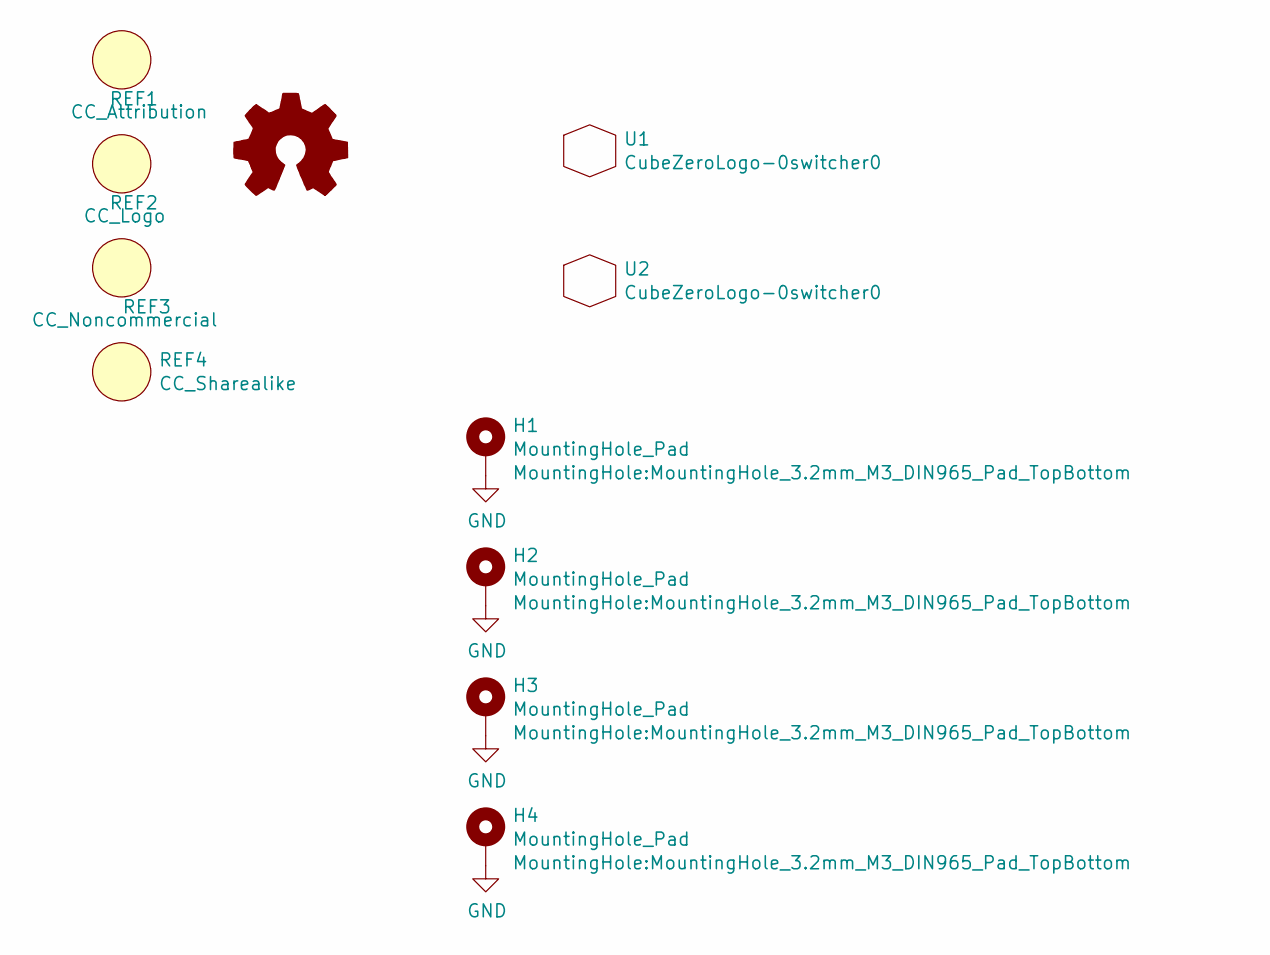
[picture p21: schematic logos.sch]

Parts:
H1, H2, H3, H4: MountingHole_Pad; MountingHole_3.2mm_M3_DIN965_Pad_TopBottom
LOGO1: Logo_Open_Hardware_Small; OSHW-Logo_11.4x12mm_SilkScreen
REF1: CC_Attribution; Symbol_CC-Attribution_Silkscreen_Small
REF2: CC_Logo; Symbol_CC_Logo_Silkscreen_small
REF3: CC_Noncommercial; Symbol_CC-Noncommercial_Silkscreen_Small
REF4: CC_Sharealike; Symbol_CC-ShareAlike_Silkscreen_Small
U1: CubeZeroLogo-0switcher0; CubeZeroLogo_Ink_And_Cu
U2: CubeZeroLogo-0switcher0; CubeZeroLogo_Silk

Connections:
GND: H1.1, H2.1, H3.1, H4.1; also elsewhere on the board

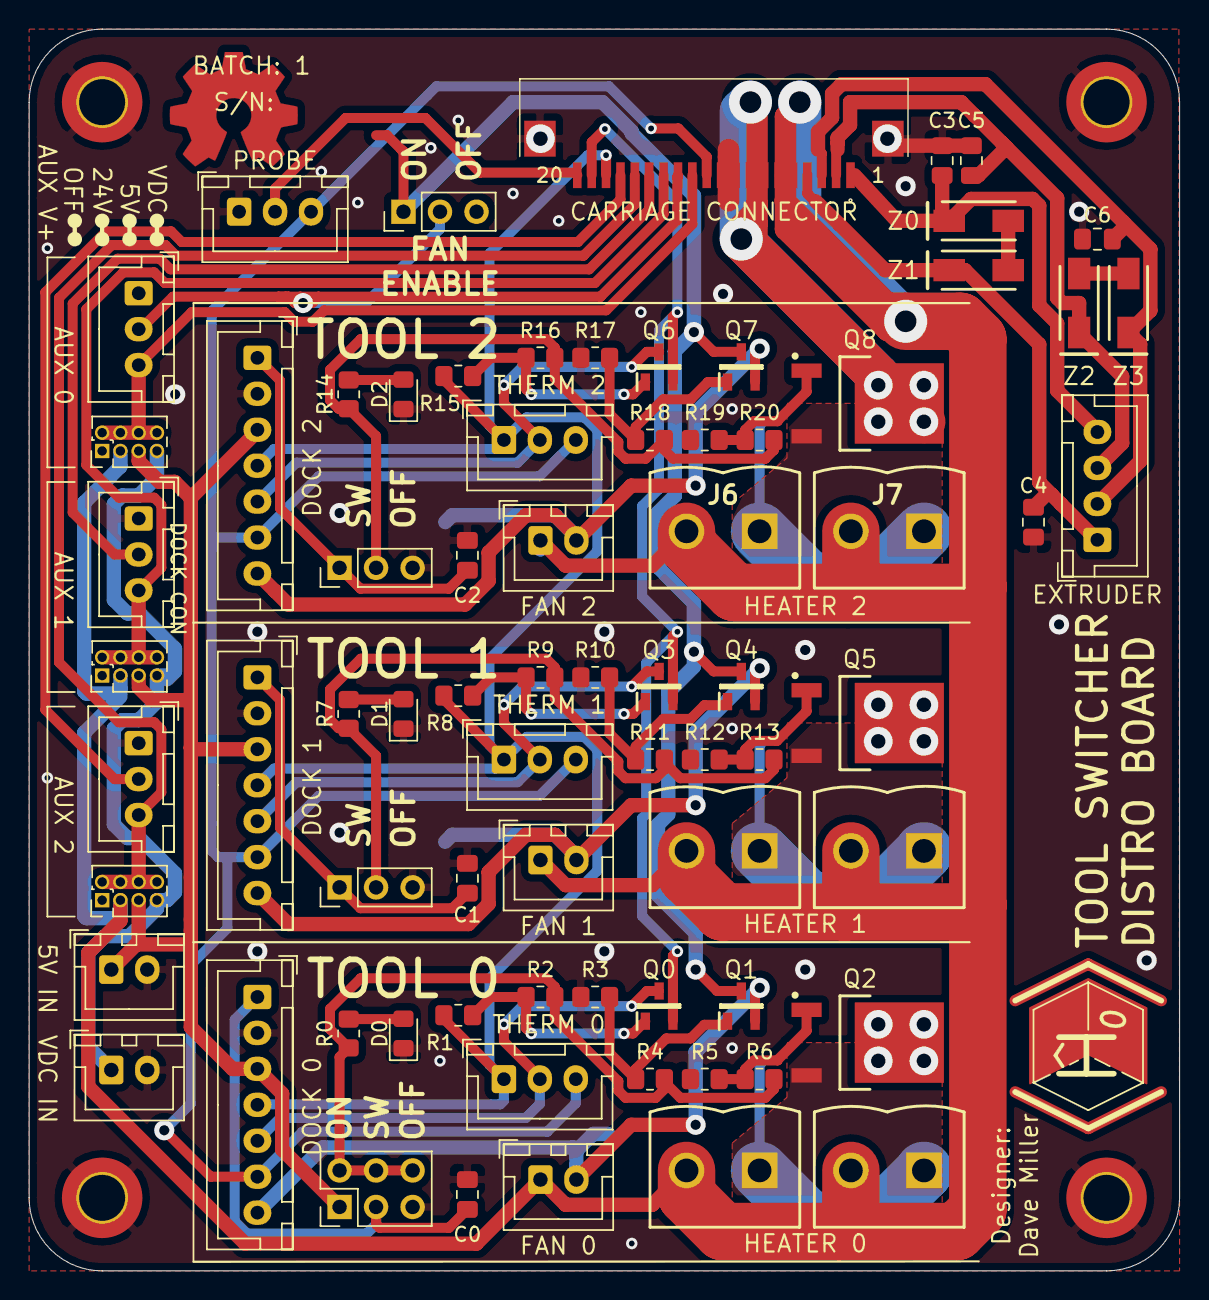
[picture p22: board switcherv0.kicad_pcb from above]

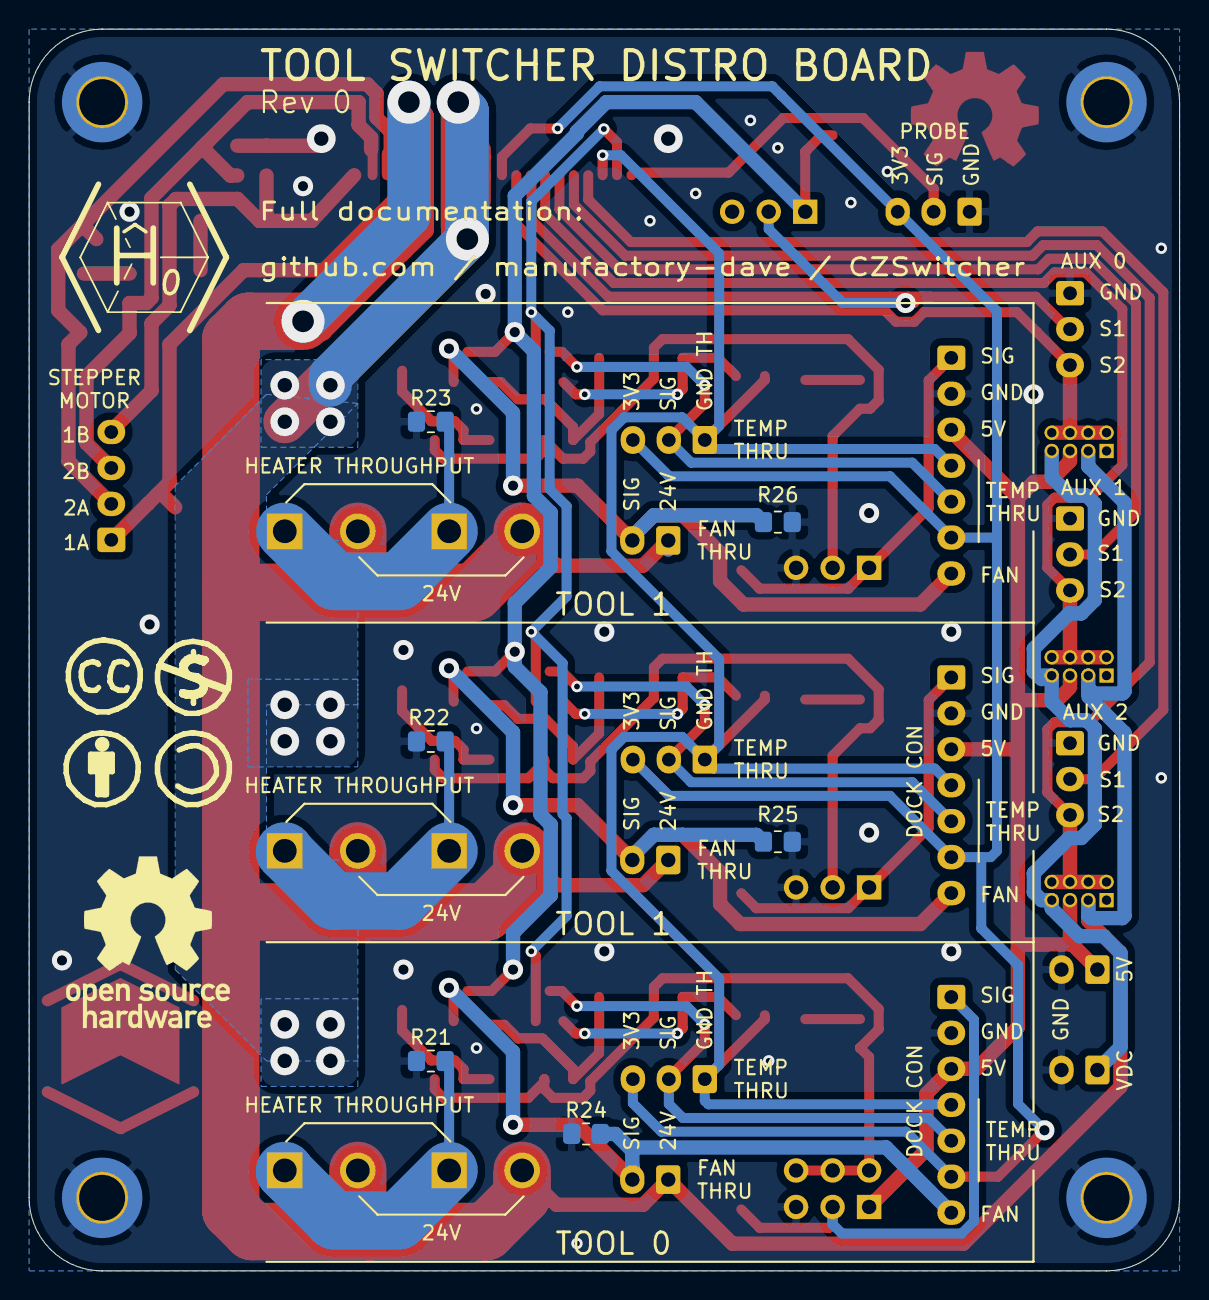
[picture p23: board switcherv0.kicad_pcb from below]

Board: 2 copper layers, 80.0 x 86.4 mm, 92 parts (12 on the bottom side), 49 nets.

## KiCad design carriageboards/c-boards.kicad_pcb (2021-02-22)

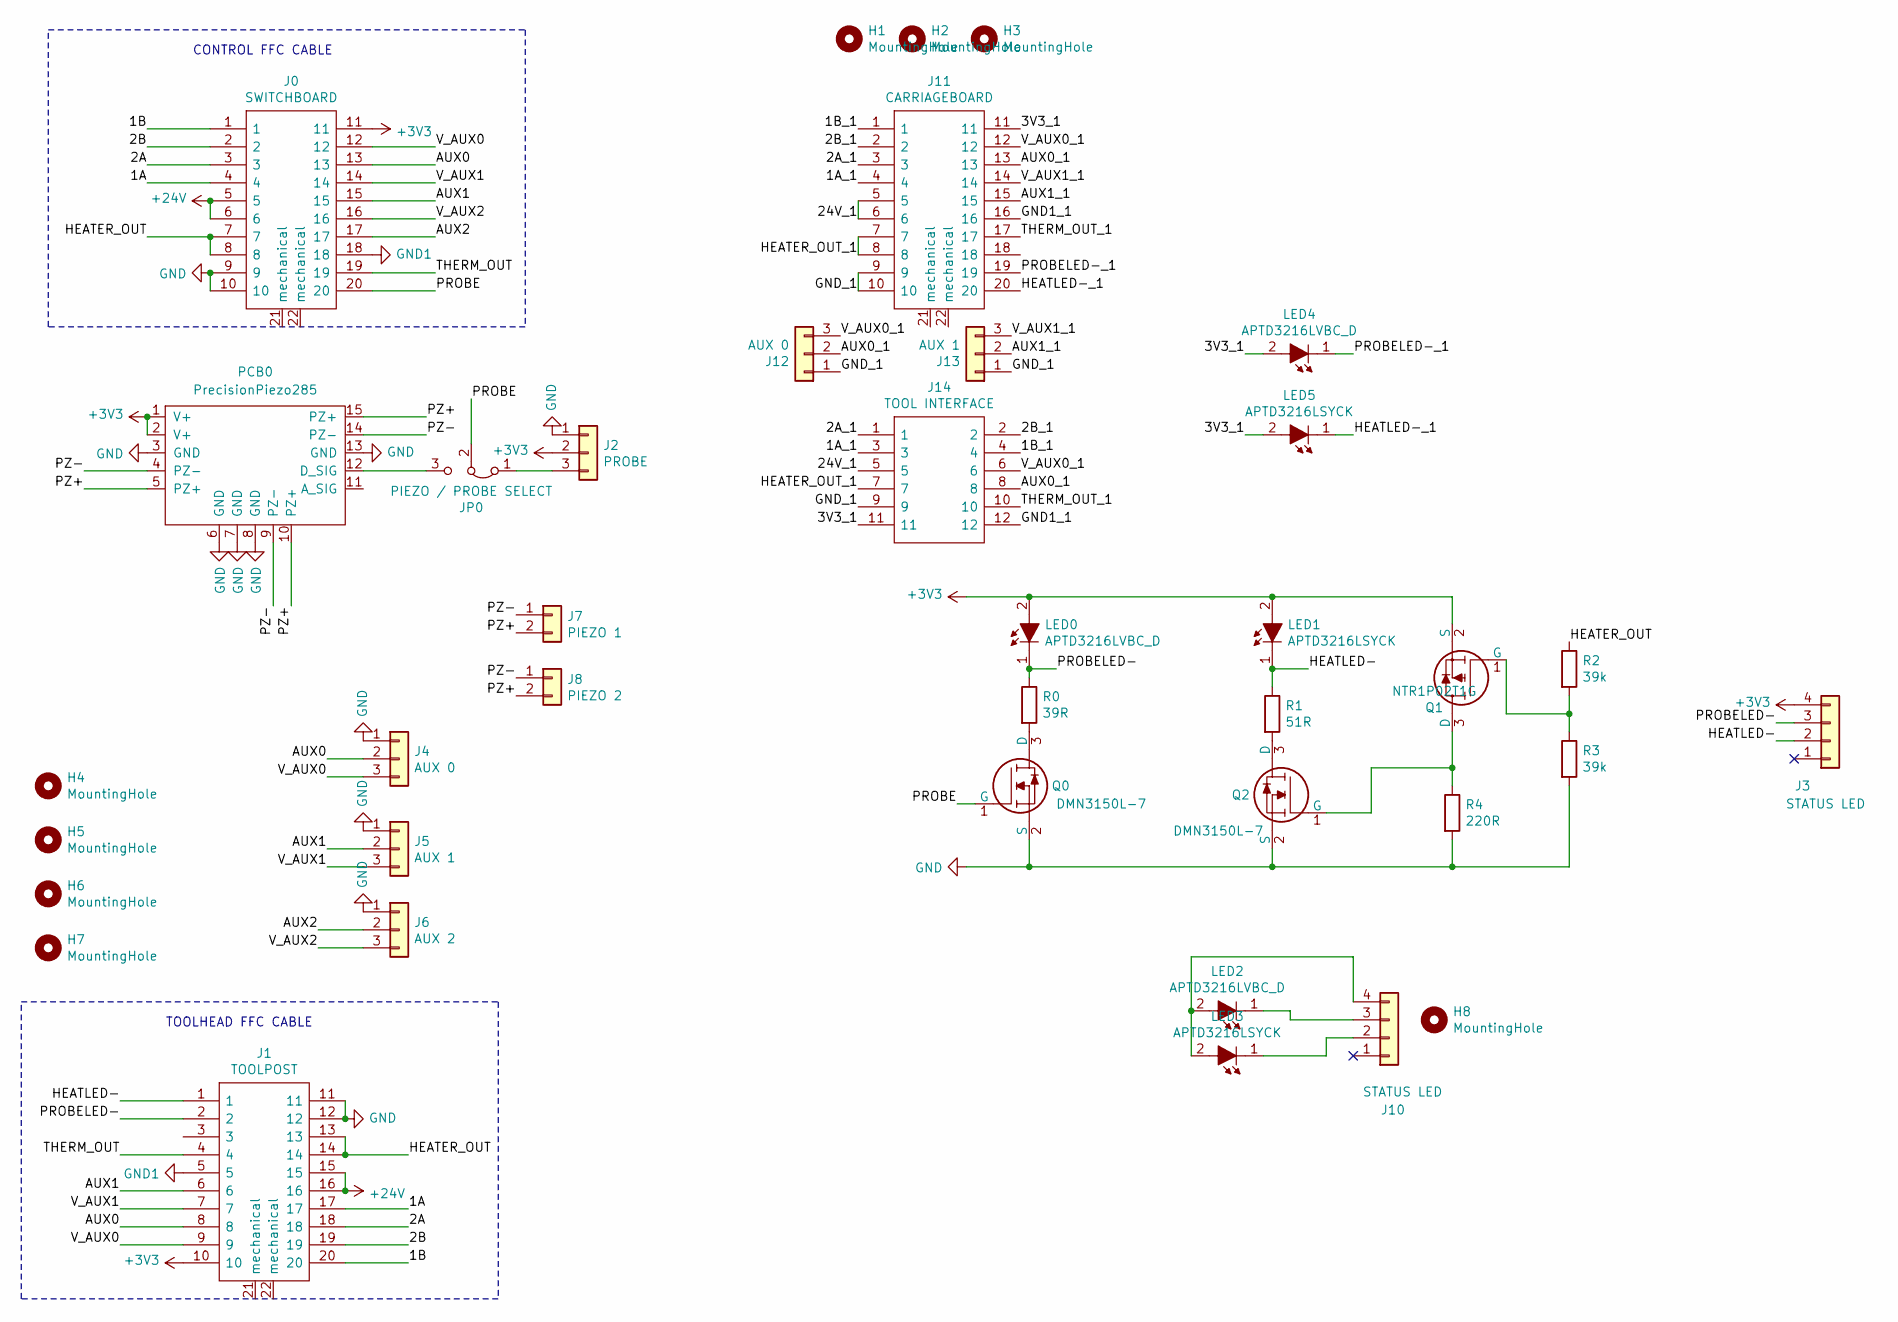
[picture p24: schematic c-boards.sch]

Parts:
H1, H2, H3, H4, H5, H6, H7, H8: MountingHole; MountingHole_2.7mm_M2.5
J0: SWITCHBOARD; ZF1-20-XX-ZZ-WT_Handsolder; Manufacturer_Part_Number ZF1-20-01-T-WT
J1: TOOLPOST; ZF1-20-XX-ZZ-WT_Handsolder; Manufacturer_Part_Number ZF1-20-01-T-WT
J2: PROBE; JST_XH_S3B-XH-A_1x03_P2.50mm_Horizontal
J3, J10: STATUS LED; JST-ZH_S4B-ZR-SM4A-TF
J4: AUX 0; JST_XH_S3B-XH-A_1x03_P2.50mm_Horizontal
J5: AUX 1; JST_XH_S3B-XH-A_1x03_P2.50mm_Horizontal
J6: AUX 2; JST_XH_S3B-XH-A_1x03_P2.50mm_Horizontal
J7: PIEZO 1; JST-ZH_S2B-ZR-SM4A-TF; Part No S2B-ZR-SM4A-TF
J8: PIEZO 2; JST-ZH_S2B-ZR-SM4A-TF; Part No S2B-ZR-SM4A-TF
J11: CARRIAGEBOARD; ZF1-20-XX-ZZ-WT_Handsolder; Manufacturer_Part_Number ZF1-20-01-T-WT
J12: AUX 0; JST-XH_2.50MM_03x01_SMT
J13: AUX 1; JST-XH_2.50MM_03x01_SMT
J14: TOOL INTERFACE; 813-S1-012-10-014101; Manufacturer_Part_Number 813-S1-012-10-014101
JP0: PIEZO / PROBE SELECT; PinHeader_1x03_P2.54mm_Vertical
LED0, LED2, LED4: APTD3216LVBC_D; LED_1206_3216Metric_Pad1.42x1.75mm_HandSolder; Manufacturer_Part_Number APTD3216LVBC/D
LED1, LED3, LED5: APTD3216LSYCK; LED_1206_3216Metric_Pad1.42x1.75mm_HandSolder; Manufacturer_Part_Number APTD3216LSYCK
PCB0: PrecisionPiezo285; Precision_Piezo_2.85
Q0, Q2: DMN3150L-7; SUPER-SOT-3; Manufacturer_Part_Number DMN3150L-7
Q1: NTR1P02T1G; SUPER-SOT-3; Manufacturer_Part_Number NTR1P02T1G
R0: 39R; R_0805_2012Metric_Pad1.20x1.40mm_HandSolder; Manufacturer_Part_Number RK73B2ATTD390J
R1: 51R; R_0805_2012Metric_Pad1.20x1.40mm_HandSolder; Manufacturer_Part_Number RK73B2ATTD510J
R2: 39k; R_0805_2012Metric_Pad1.20x1.40mm_HandSolder; Manufacturer_Part_Number RK73B2ATTD393J
R3: 39k; R_0805_2012Metric_Pad1.20x1.40mm_HandSolder; Manufacturer_Part_Number RK73B2ATTD103J
R4: 220R; R_0805_2012Metric_Pad1.20x1.40mm_HandSolder; Manufacturer_Part_Number RK73B2ATTD510J

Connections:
+3V3: J0.11, J1.10, J2.2, J3.4, LED0.2, LED1.2, PCB0.1 (V+), PCB0.2 (V+), Q1.2 (S)
+24V: J0.5, J0.6, J1.15, J1.16
/1A: J0.4, J1.17
/1A_1: J11.4, J14.3
/1B: J0.1, J1.20
/1B_1: J11.1, J14.4
/2A: J0.3, J1.18
/2A_1: J11.3, J14.1
/2B: J0.2, J1.19
/2B_1: J11.2, J14.2
/3V3_1: J11.11, J14.11, LED4.2, LED5.2
/24V_1: J11.5, J11.6, J14.5
/AUX0: J0.13, J1.8, J4.2
/AUX0_1: J11.13, J12.2, J14.8
/AUX1: J0.15, J1.6, J5.2
/AUX1_1: J11.15, J13.2
/AUX2: J0.17, J6.2
/GND1_1: J11.16, J14.12
/GND_1: J11.9, J11.10, J12.1, J13.1, J14.9
/HEATER_OUT: J0.7, J0.8, J1.13, J1.14, R2.1
/HEATER_OUT_1: J11.7, J11.8, J14.7
/HEATLED-: J1.1, J3.2, LED1.1, R1.1
/HEATLED-_1: J11.20, LED5.1
/PROBE: J0.20, JP0.2 (C), Q0.1 (G)
/PROBELED-: J1.2, J3.3, LED0.1, R0.1
/PROBELED-_1: J11.19, LED4.1
/PZ+: J7.2, J8.2, PCB0.5 (PZ+), PCB0.10 (PZ+), PCB0.15 (PZ+)
/PZ-: J7.1, J8.1, PCB0.4 (PZ-), PCB0.9 (PZ-), PCB0.14 (PZ-)
/THERM_OUT: J0.19, J1.4
/THERM_OUT_1: J11.17, J14.10
/V_AUX0: J0.12, J1.9, J4.3
/V_AUX0_1: J11.12, J12.3, J14.6
/V_AUX1: J0.14, J1.7, J5.3
/V_AUX1_1: J11.14, J13.3
/V_AUX2: J0.16, J6.3
GND: J0.9, J0.10, J1.11, J1.12, J2.1, J4.1, J5.1, J6.1, PCB0.3 (GND), PCB0.6 (GND), PCB0.7 (GND), PCB0.8 (GND), PCB0.13 (GND), Q0.2 (S), Q2.2 (S), R3.2, R4.2
GND1: J0.18, J1.5
unnamed: J2.3, JP0.1 (A)
unnamed: J10.2, LED3.1
unnamed: J10.3, LED2.1
unnamed: J10.4, LED2.2, LED3.2
unnamed: JP0.3 (B), PCB0.12 (D_SIG)
unnamed: Q0.3 (D), R0.2
unnamed: Q1.1 (G), R2.2, R3.1
unnamed: Q1.3 (D), Q2.1 (G), R4.1
unnamed: Q2.3 (D), R1.2

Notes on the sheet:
CONTROL FFC CABLE
TOOLHEAD FFC CABLE

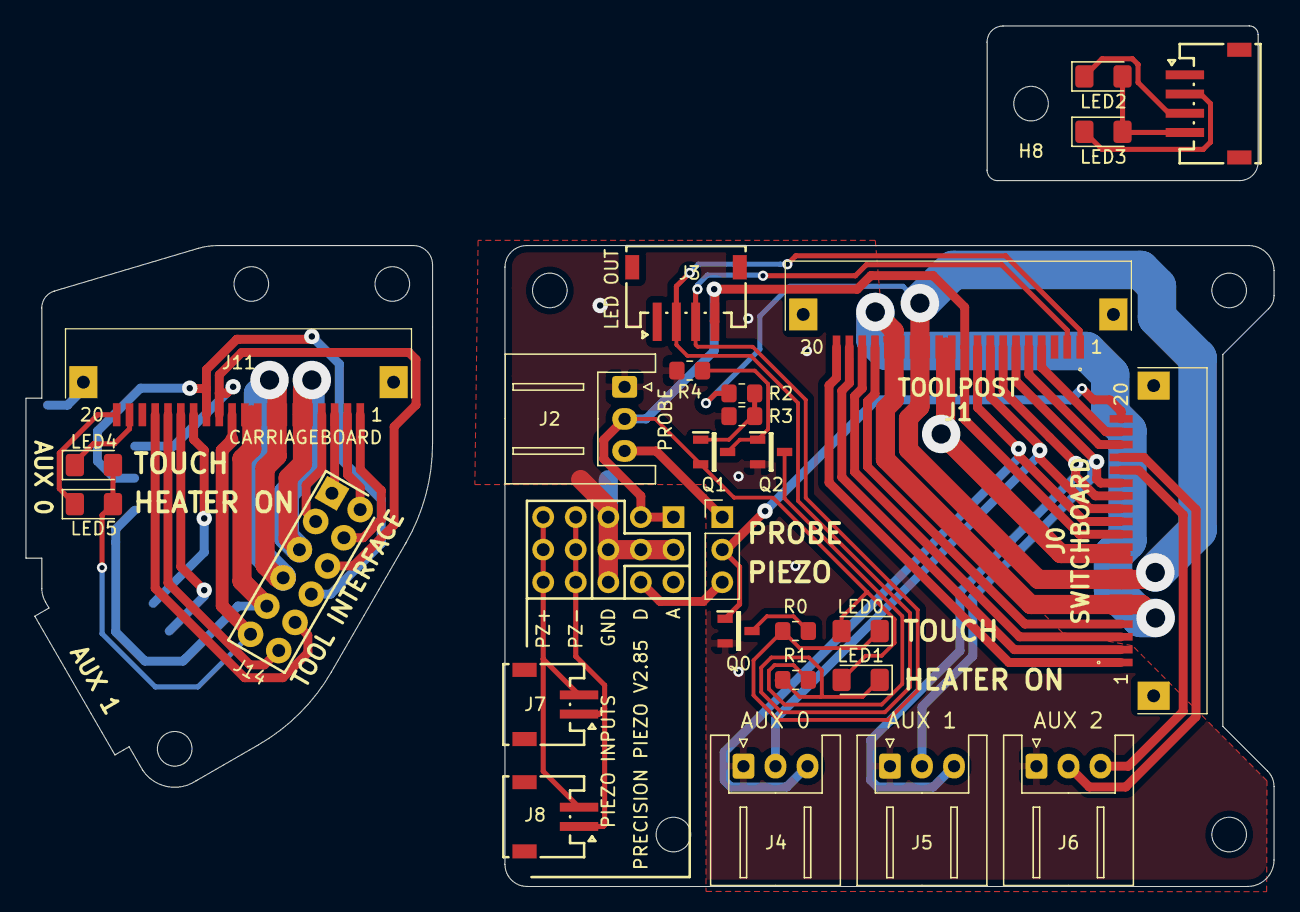
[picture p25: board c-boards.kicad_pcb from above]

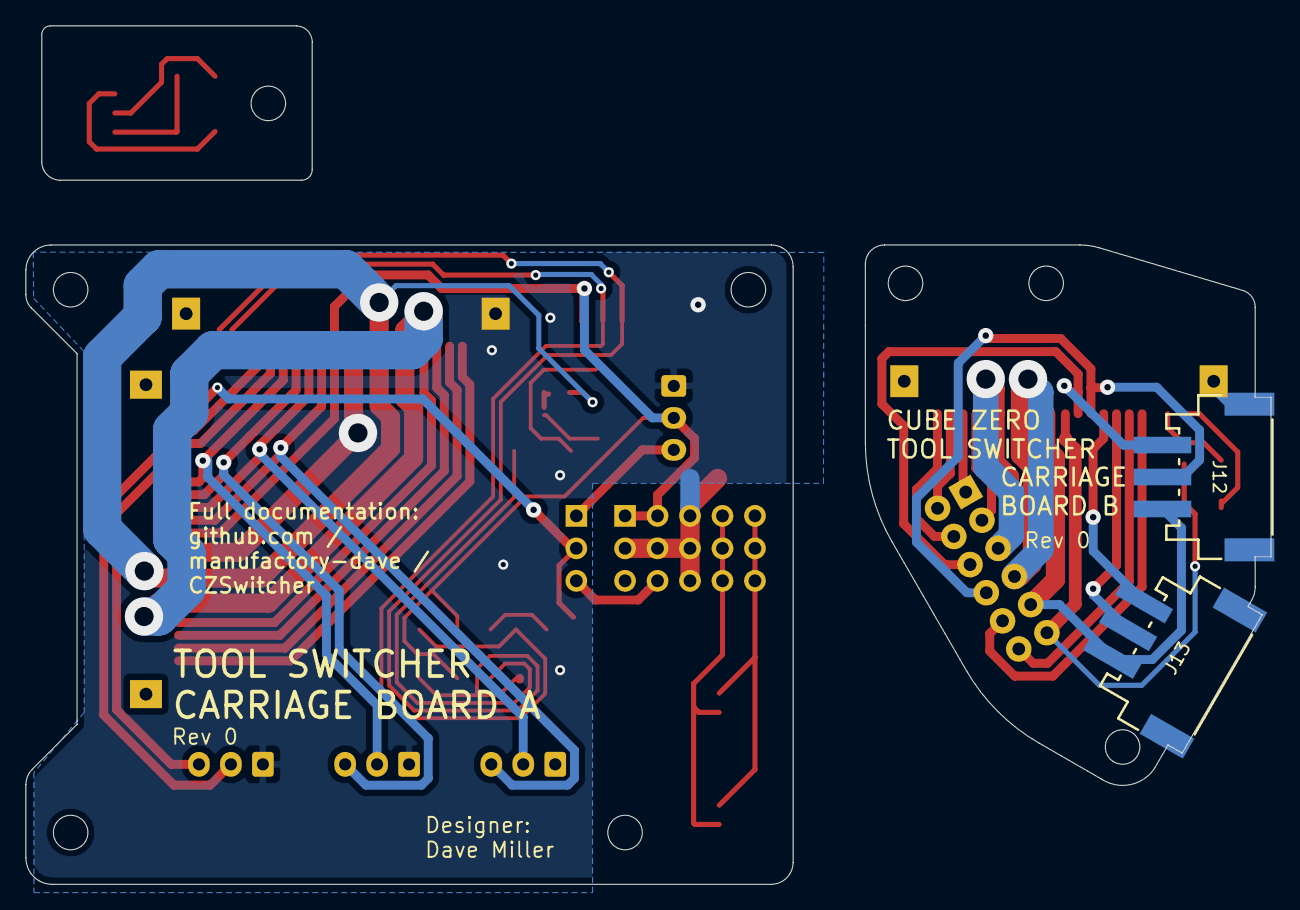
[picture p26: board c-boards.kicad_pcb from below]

Board: 2 copper layers, 97.4 x 67.1 mm, 38 parts (2 on the bottom side), 46 nets.

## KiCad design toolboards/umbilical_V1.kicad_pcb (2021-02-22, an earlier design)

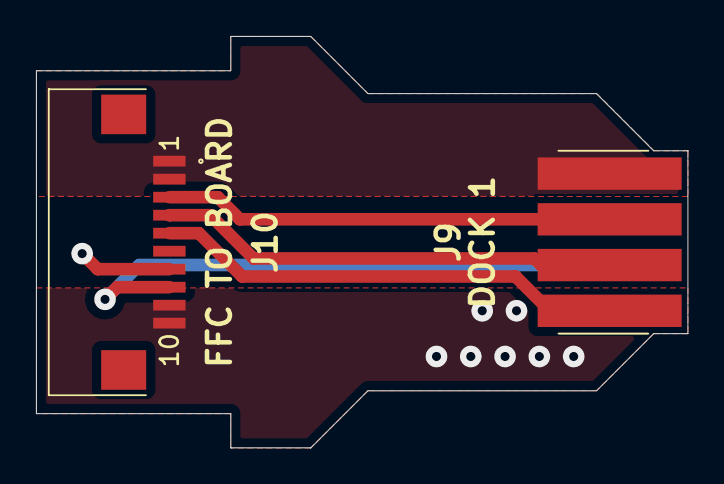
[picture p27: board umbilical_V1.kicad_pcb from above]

Board: 2 copper layers, 36.2 x 22.9 mm, 3 parts (1 on the bottom side), 7 nets.

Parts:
J9: DOCK 1; 8MM11000402131_handsolder
J10: FFC TO BOARD; ZF1-10-XX-ZZ-WT-TR
J11: DOCK 2; 8MM11000402131_handsolder

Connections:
/3V3_2: J9.3, J10.4
/24V_2: J9.1, J10.1, J10.2
/AUX0_2: J9.4, J10.5
/GND1_2: J9.2, J10.3
/GND_2: J10.7, J11.3
/HEATER_OUT_2: J10.9, J10.10, J11.1
/THERM_OUT_2: J10.8, J11.2
